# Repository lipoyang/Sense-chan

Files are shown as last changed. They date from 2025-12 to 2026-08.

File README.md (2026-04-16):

# ｾﾝｽﾁｬﾝ (Sense-chan)
ｾﾝｽﾁｬﾝはｽﾀｯｸﾁｬﾝ派生のSPRESENSEマイコン搭載ロボットです。  
SPRESENSE搭載のロボット用基板と対向2輪型ロボットおよびそのソフトウェアで構成されます。

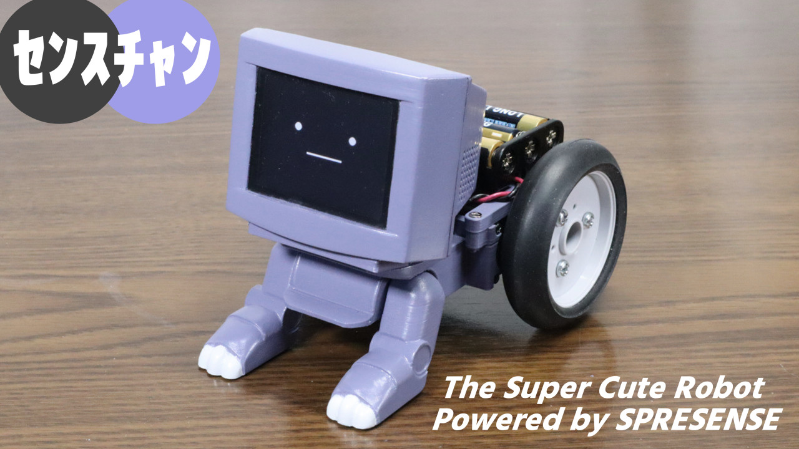
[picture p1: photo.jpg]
写真


## 解説

* [センスチャン ～ ｽﾀｯｸﾁｬﾝ派生のSPRESENSE搭載ロボット ～ by lipoyang | elchika](https://elchika.com/article/c5d4bbd1-0e7f-4fa6-907b-d6d020c664f9)

## ファイル
* [firmware](./firmware/) : ファームウェアのソースコード
* [mechanical](./mechanical/) : メカ部品のSTEPファイルとSTLファイル
* [board](./board/) : プリント基板の回路図とパターン設計

## SDカードにコピーするファイル

下記のファイルをマイクロSDカードにコピーして、ｾﾝｽﾁｬﾝのマイクロSDカードスロットに挿入してください。
* [fs_efont_ja_16.bin](./firmware/Sense-chan/sd_data/fs_efont_ja_16.bin) : フォントデータ
* [config.json](./firmware/Sense-chan/sd_data/config.json) : 設定ファイル

## 原典
このプロジェクトはｽﾀｯｸﾁｬﾝにインスパイアされた派生作品です。[ｽﾀｯｸﾁｬﾝ](https://github.com/stack-chan/stack-chan)は[ししかわ](https://x.com/stack_chan)さんが開発、公開している、 手乗りサイズのｽｰﾊﾟｰｶﾜｲｲコミュニケーションロボットです。

また、[B-SKY-Lab](https://x.com/eternalfriend17)さんが開発、公開している[ﾀｲﾘﾝﾁｬﾝ](https://github.com/kim-xps12/bsl-balancer)の機構設計やソフトウェアを一部参考にしています。

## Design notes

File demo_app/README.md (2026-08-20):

# デモ用Webアプリ
- ｾﾝｽﾁｬﾝのデモ用のWebアプリです。
- Web Bluetooth API に対応したChrome系のブラウザで動作します。
- iOS版のChromeには対応していません。
- UIのデザインに 源暎エムゴv2 フォントを使用しています。
- 源暎エムゴv2 フォントは SIL Open Font License 1.1 の下で提供されています。

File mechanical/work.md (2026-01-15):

# 作業メモ

## 3Dプリンタ出力
- 3Dプリンタ : Bambu Lab A1 mini
- フィラメント : PLA

## 追加工
- M2ネジの下穴はφ1.7で設計したが、3Dプリンタでは穴が細るので、ピンバイスを用いφ1.7のドリルでリワーク
- M3ネジの下穴はφ2.5で設計したが、3Dプリンタでは穴が細るので、ピンバイスを用いφ2.5のドリルでリワーク
- M2ネジのバカ穴は、細ることを見越してφ2.2で設計したがそれでも細いので、ピンバイスを用いφ2.0のドリルでリワーク
- 前脚の六角軸と本体の六角穴は、軸が太って穴が細ることを見越してマージンを設けたが、それでも嵌まらなかったので、六角軸を平ヤスリでリワーク
- 電池ボックスの固定穴(バカ穴)はネジ頭が電池に干渉するので、ボール盤を用いφ6.0のドリルで座グリ
- 電池ボックス固定プレートの本体取り付けネジはネジ頭が電池ボックスと干渉するので(設計ミス)、ボール盤を用いφ4.0で座グリして、皿ネジで取り付ける

## 表面処理と塗装
- 積層痕はヤスリがけでなるべく整形する
- いちじるしく段差が目立つ箇所についてはパテで埋めてヤスリがけ
- サーフェイサーを吹いて下地を整える
- 水性ホビーカラーで塗装
  - XHUG09 ミカエリス パープル
  - HUG104 ディアクティブ ホワイト 

## パネル
- デザインの都合でLCDパネルより筐体の開口部が大きいため、そのままでは見映えが悪い
- アクリサンデーの厚さ1mmの強化透明アクリル板を47mm×36mmにカット
- 裏面から黒枠を塗装し、透明部が42mm×32mmとなるようにする
- このパネルを筐体の開口部にはめ込む

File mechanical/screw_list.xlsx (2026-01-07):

使用箇所 | 個数 | 径 | 長さ | その他
ｾﾝｽﾁｬﾝ基板固定 | 4 | M2 | 4
頭部前後固定 | 4 | M2 | 5
首固定 | 2 | M2 | 8
前脚固定 | 2 | M2 | 4
前脚補強 | 2 | M2 | 15
電池ボックスプレート固定 | 4 | M2 | 8 | 皿ネジ
電池ボックス固定 | 2 | M3 | 5 | 皿ネジ
サーボ固定 | 8 | M2 | 8 | サーボの付属品
サーボホーン固定 | 8 | M2 | 6 | サーボの付属品
ホイール固定 | 6 | M3 | 8 | タイヤの付属品

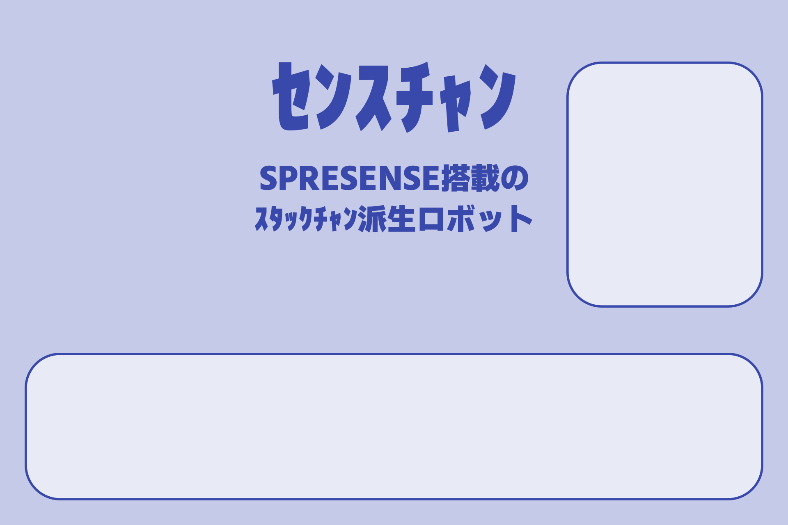
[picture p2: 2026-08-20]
demo_app/background.png

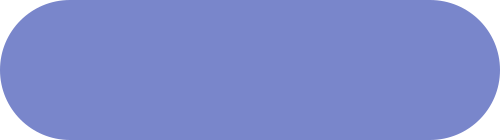
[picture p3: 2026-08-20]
demo_app/button_lowkey.png

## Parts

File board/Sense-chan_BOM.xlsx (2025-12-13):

Reference | Qty | Part Number | Description | Supplier | Supplier Code
C1, C3, C4, C6, C7, C9, C10, C11, C12, C14, C15, C16 | 12 | 0.1uF | 1608 (0603) | (在庫) | (generic)
C8, C17 | 1 | 1uF | 1608 (0603) | (在庫) | (generic)
C2, C5 | 2 | 22uF | 3216(1206) | (在庫) | (generic)
C13 | 1 | 47uF | 3216(1206) | (在庫) | (generic)
R1 | 1 | 62kΩ, class F | 1608 (0603) | digikey | 10-ERJ-U03F6202VCT-ND
R3 | 1 | 10kΩ, class F | 1608 (0603) | digikey | 10-ERJ-U03F1002VCT-ND
R2, R7 | 2 | 180kΩ | 1608 (0603) | (在庫) | (generic)
R4 | 1 | 10Ω | 1608 (0603) | (在庫) | (generic)
R5 | 1 | 47Ω | 1608 (0603) | (在庫) | (generic)
R6, R8, R9, R12 | 4 | 10kΩ | 1608 (0603) | (在庫) | (generic)
R10 | 1 | 100Ω | 1608 (0603) | (在庫) | (generic)
R11 | 1 | 2.2kΩ | 1608 (0603) | (在庫) | (generic)
RN1, RN2, RN3, RN4 | 4 | 1kΩ×4素子 EXB-38V102JV | 1608 (0603)×4素子, 凸型 | digikey | Y9102CT-ND
D1 | 1 | SS2040FL | D_SOD-123 | (在庫, 秋月) | 102073
J1, J7 | 2 | B3B-EH-A | 日圧EH3ピン(トップ型) | (在庫, 共立) | 5CP14I
J2 | 1 | LCD Flexible Cable | 0.8mmピッチ 12ピン | - | -
J3 | 1 | DF40HC(3.0)-100DS-0.4V | SPRESENSE B2Bコネクタ | digikey | 26-DF40HC(3.0)-100DS-0.4V(51)CT-ND
J4 | 1 | DM3AT | ヒロセ microSDカードスロット | digikey | 26-DM3AT-SF-PEJM5(11)CT-ND
J5, J6 | 2 | B4B-EH-A | 日圧EH4ピン(トップ型) | (在庫, 共立) | 5CP14J
Q1 | 1 | IRFML8244TRPBF | SOT-23 | (在庫, digikey) | IRFML8244TRPBFCT-ND
U1 | 1 | TC1262-3.3VDB | SOT-223-3_TabPin2 | (在庫, digikey) | TC1262-3.3VDB-ND
U2, U3 | 2 | LSF0108PWR | PW0020A | digikey | 296-37828-1-ND
U4 | 1 | SN74LV1T126DBVR | SOT-23-5 | digikey | 296-37174-1-ND
U5 | 1 | SN74LV1T125DBVR | SOT-23-5 | digikey | 296-37172-1-ND

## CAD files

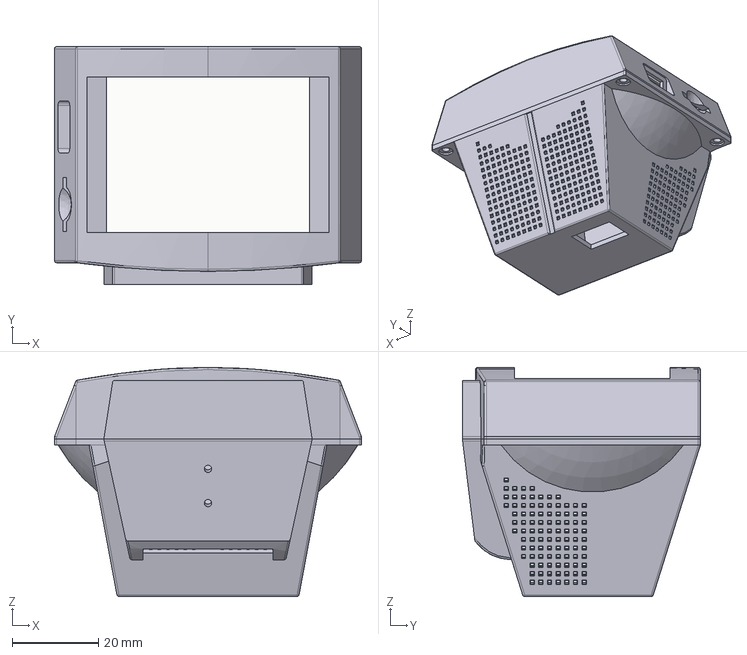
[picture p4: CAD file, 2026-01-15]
mechanical/STEP/VaioMonitor.step
71.0 x 55.0 x 53.0 mm

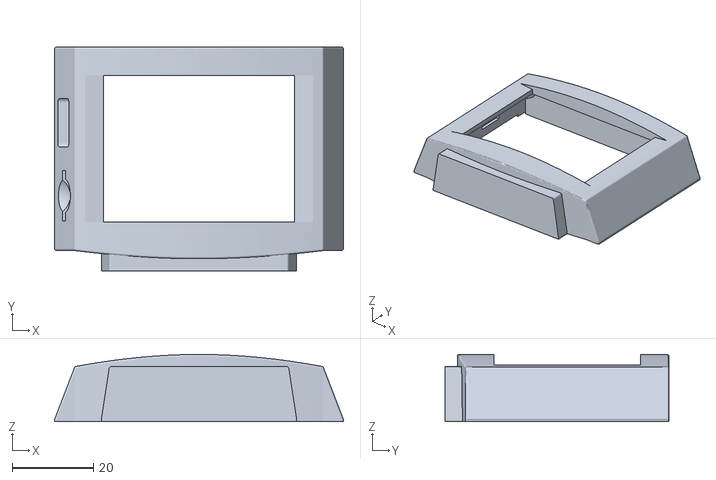
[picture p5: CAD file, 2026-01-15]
mechanical/STL/VaioMonitor_frame.stl
71.0 x 55.0 x 16.5

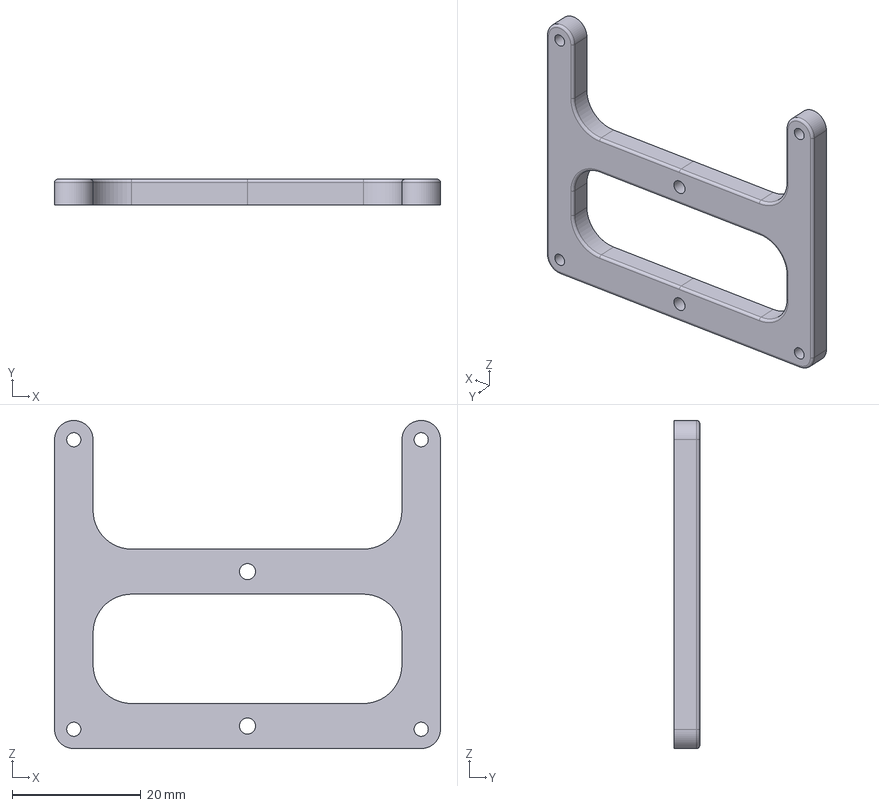
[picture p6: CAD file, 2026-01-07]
mechanical/STEP/RearPlate.step
60.0 x 4.00 x 51.0 mm

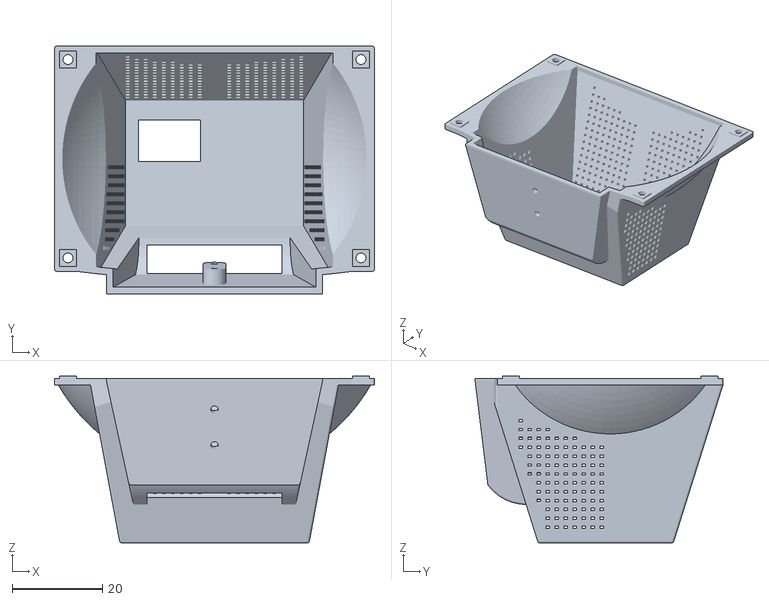
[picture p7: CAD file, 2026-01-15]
mechanical/STL/VaioMonitor_back.stl
71.0 x 55.0 x 37.0

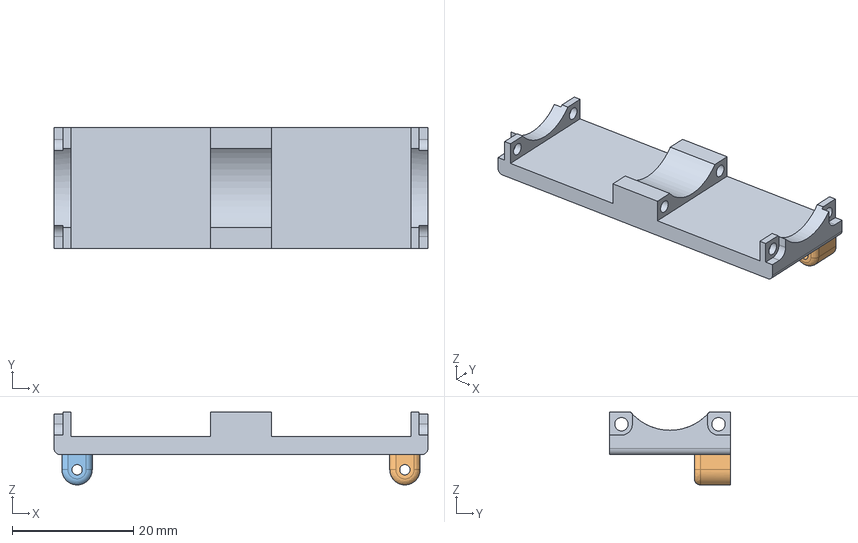
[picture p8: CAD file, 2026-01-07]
mechanical/STEP/RearBracket.step
61.6 x 20.0 x 12.0 mm

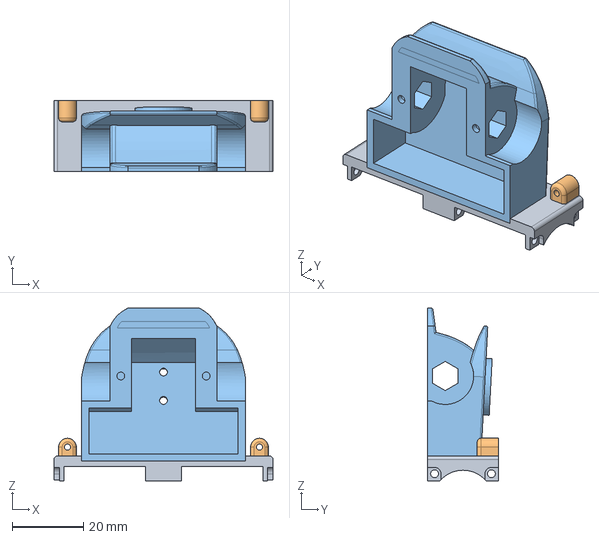
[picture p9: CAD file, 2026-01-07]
mechanical/STEP/Body.step
61.6 x 20.0 x 48.6 mm

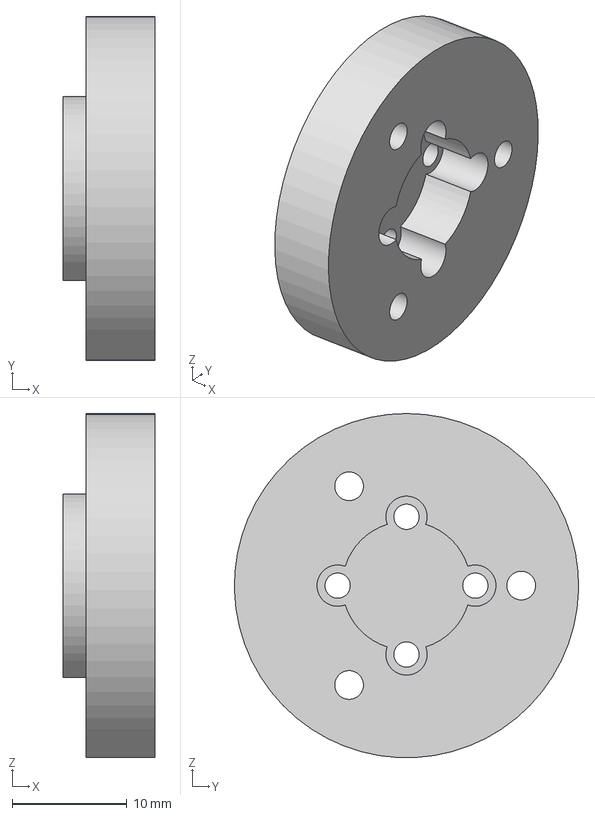
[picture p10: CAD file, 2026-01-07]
mechanical/STEP/WheelAdaptor.step
8.00 x 30.0 x 30.0 mm

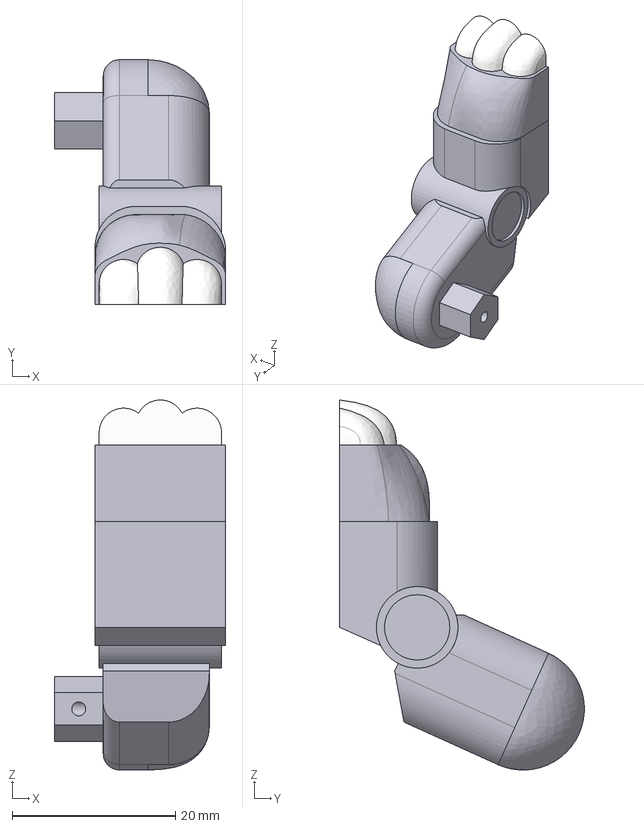
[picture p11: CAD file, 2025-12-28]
mechanical/STEP/LegL.step
21.0 x 30.0 x 45.4 mm

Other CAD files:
mechanical/STEP/LegR.step
mechanical/STL/Body.stl
mechanical/STL/LegL.stl
mechanical/STL/LegR.stl
mechanical/STL/RearBracket.stl
mechanical/STL/RearPlate.stl
mechanical/STL/WheelAdaptor.stl
mechanical/Sense-chan.f3d

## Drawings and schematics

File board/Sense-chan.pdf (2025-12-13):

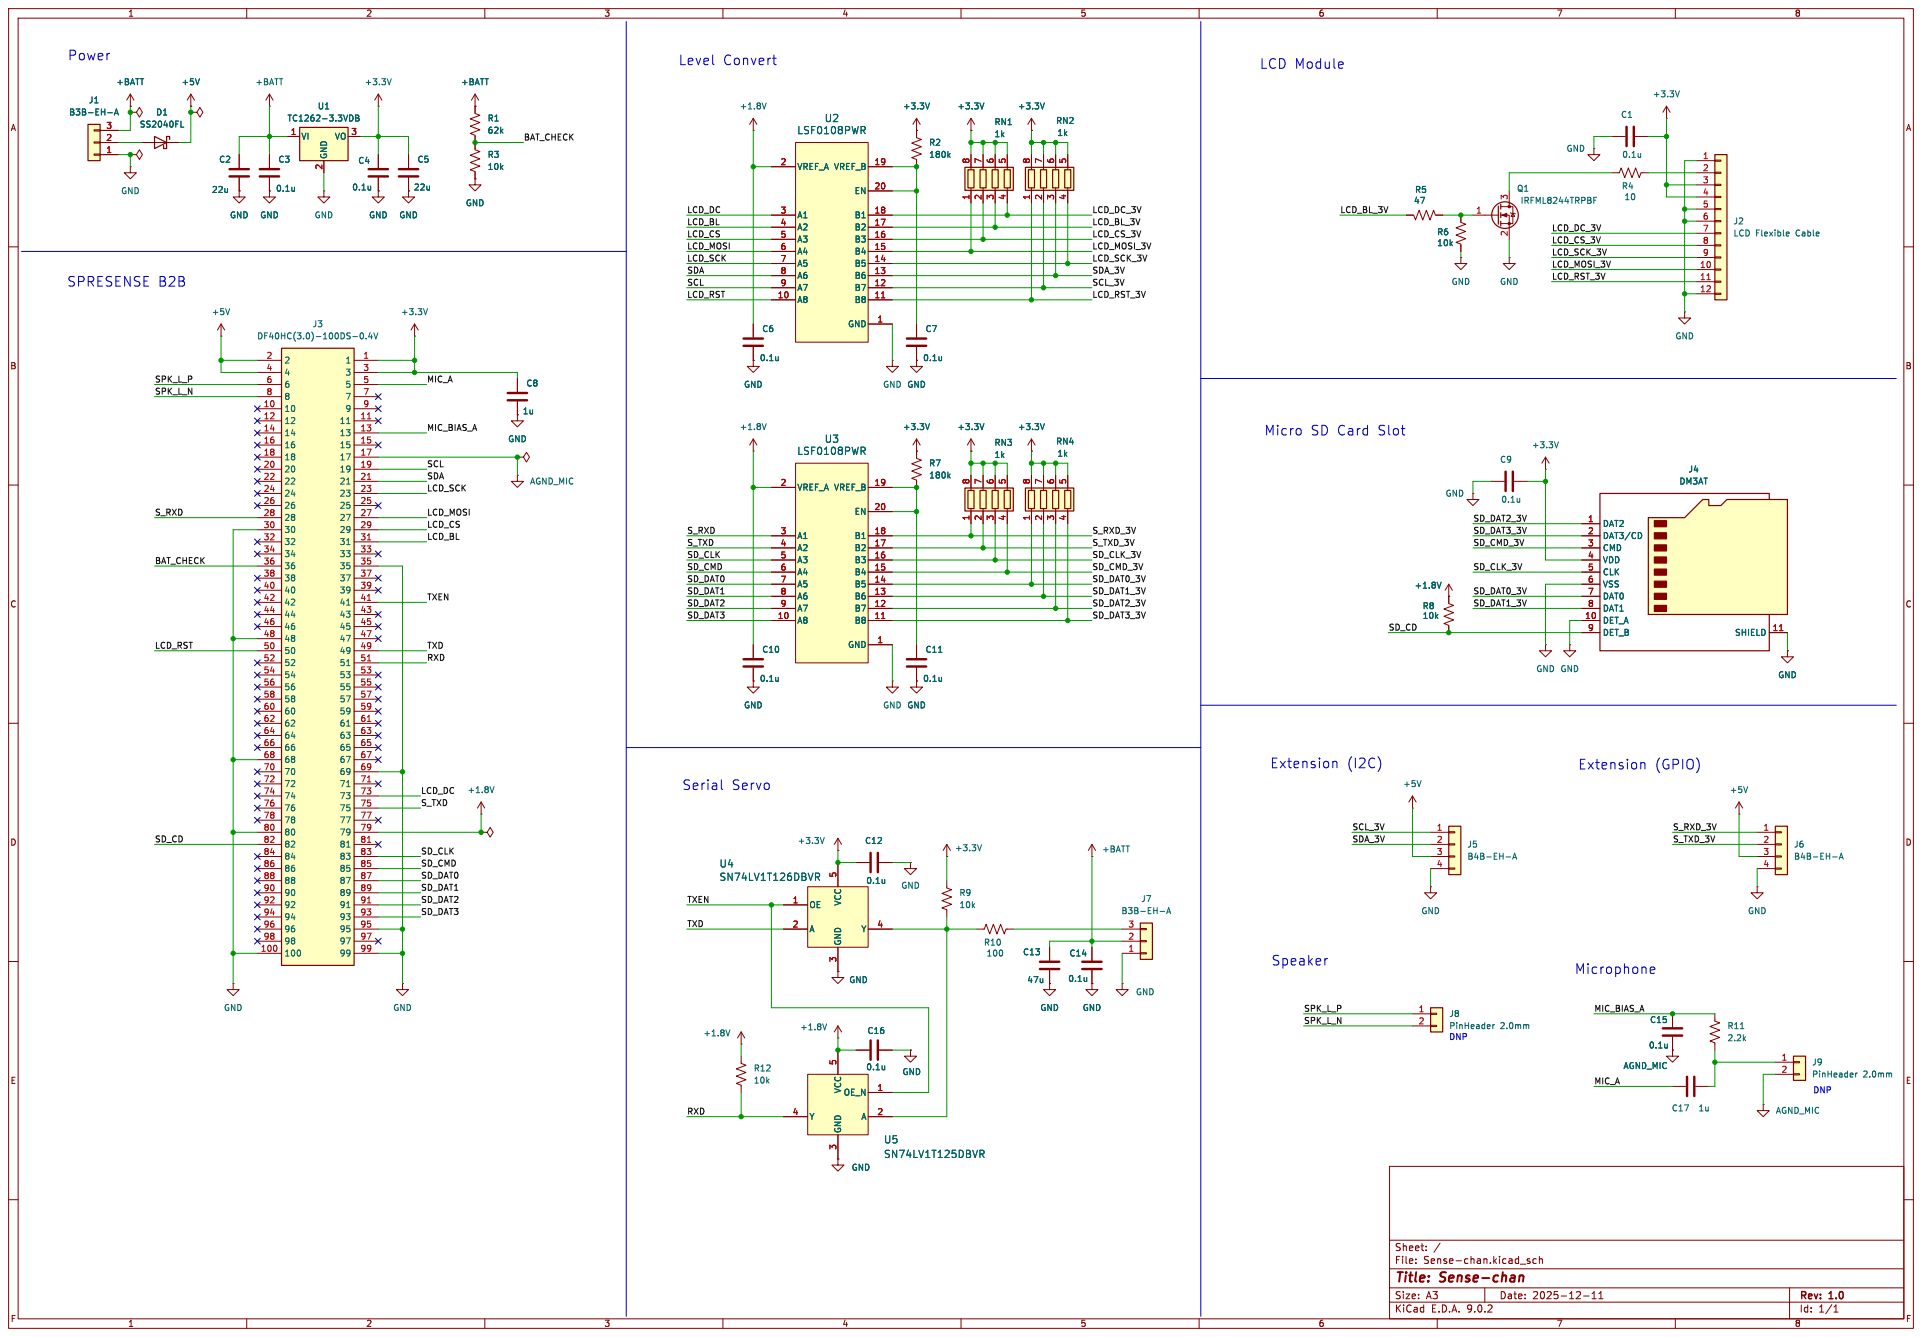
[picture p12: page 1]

Micro SD Card Slot

Extension (GPIO) DNP Speaker

File: Sense-chan.kicad_sch Sheet: /
Id: 1/1 Title: Sense-chan

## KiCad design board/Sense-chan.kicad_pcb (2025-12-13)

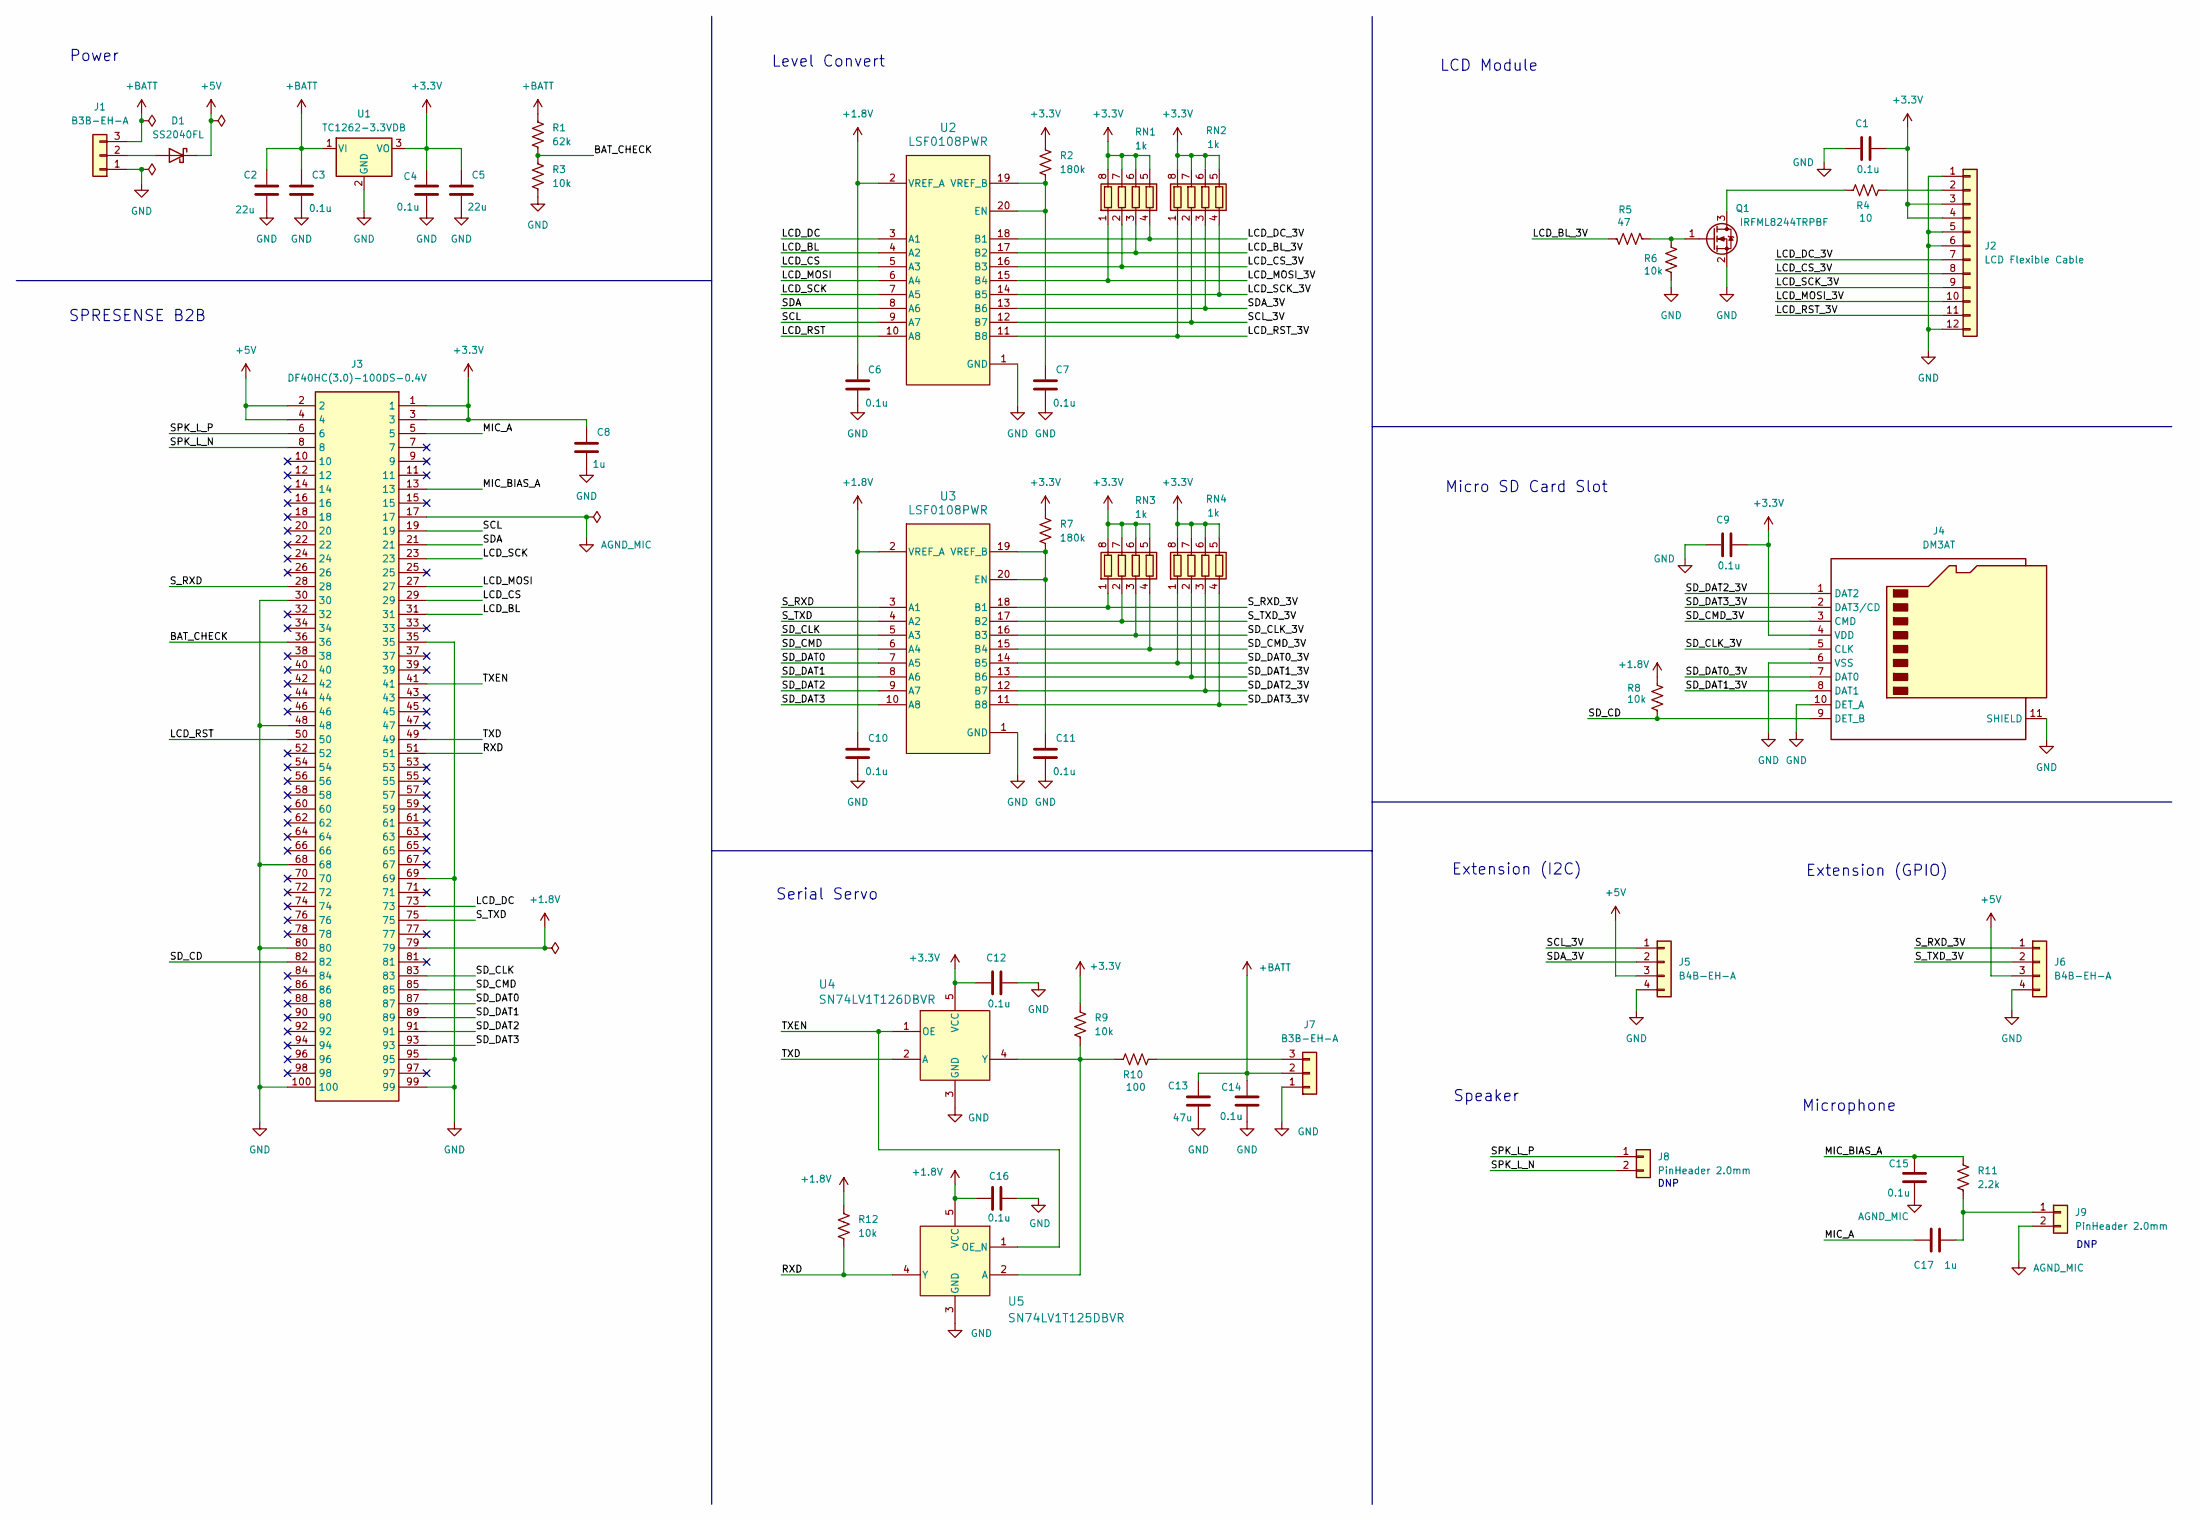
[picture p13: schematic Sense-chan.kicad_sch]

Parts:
C1, C3, C4, C6, C7, C9, C10, C11, C12, C14, C15, C16: 0.1u; C_0603_1608Metric; LCSC C14663
C2, C5: 22u; C_1206_3216Metric
C8: 1u; C_0603_1608Metric
C13: 47u; C_1206_3216Metric
C17: 1u; C_0603_1608Metric; LCSC C14663
D1: SS2040FL; D_SOD-123
J1, J7: B3B-EH-A; JST_EH_B3B-EH-A_1x03_P2.50mm_Vertical
J2: LCD Flexible Cable; LCD-Flex12-0.8mm
J3: DF40HC(3.0)-100DS-0.4V; spresense; Manufacturer_Part_Number DF40HC(3.0)-100DS-0.4V(51)
J4: DM3AT; microSD_HC_Hirose_DM3AT-SF-PEJM5
J5, J6: B4B-EH-A; JST_EH_B4B-EH-A_1x04_P2.50mm_Vertical
J8, J9: PinHeader 2.0mm; PinHeader_1x02_P2.00mm_Vertical
Q1: IRFML8244TRPBF; SOT-23
R1: 62k; R_0603_1608Metric
R2, R7: 180k; R_0603_1608Metric
R3, R6, R8, R9, R12: 10k; R_0603_1608Metric
R4: 10; R_0603_1608Metric
R5: 47; R_0603_1608Metric
R10: 100; R_0603_1608Metric
R11: 2.2k; R_0603_1608Metric
RN1, RN2, RN3, RN4: 1k; R_Array_Convex_4x0603
U1: TC1262-3.3VDB; SOT-223-3_TabPin2
U2, U3: LSF0108PWR; PW0020A
U4: SN74LV1T126DBVR; SOT-23-5
U5: SN74LV1T125DBVR; SOT-23-5

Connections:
+1.8V: C6.1, C10.1, C16.1, J3.79, R8.1, R12.1, U2.2 (VREF_A), U3.2 (VREF_A), U5.5 (VCC)
+3.3V: C1.2, C4.1, C5.1, C8.1, C9.2, C12.1, J2.3, J2.4, J3.1, J3.3, J4.4 (VDD), R2.1, R7.1, R9.1, RN1.5 (R4.2), RN1.6 (R3.2), RN1.7 (R2.2), RN1.8 (R1.2), RN2.5 (R4.2), RN2.6 (R3.2), RN2.7 (R2.2), RN2.8 (R1.2), RN3.5 (R4.2), RN3.6 (R3.2), RN3.7 (R2.2), RN3.8 (R1.2), RN4.5 (R4.2), RN4.6 (R3.2), RN4.7 (R2.2), RN4.8 (R1.2), U1.3 (VO), U4.5 (VCC)
+5V: D1.1 (K), J3.2, J3.4, J5.3, J6.3
+BATT: C2.1, C3.1, C13.1, C14.1, J1.3, J7.2, R1.1, U1.1 (VI)
/BAT_CHECK: J3.36, R1.2, R3.1
/LCD_BL: J3.31, U2.4 (A2)
/LCD_BL_3V: R5.1, RN1.3 (R3.1), U2.17 (B2)
/LCD_CS: J3.29, U2.5 (A3)
/LCD_CS_3V: J2.8, RN1.2 (R2.1), U2.16 (B3)
/LCD_DC: J3.73, U2.3 (A1)
/LCD_DC_3V: J2.7, RN1.4 (R4.1), U2.18 (B1)
/LCD_MOSI: J3.27, U2.6 (A4)
/LCD_MOSI_3V: J2.10, RN1.1 (R1.1), U2.15 (B4)
/LCD_RST: J3.50, U2.10 (A8)
/LCD_RST_3V: J2.11, RN2.1 (R1.1), U2.11 (B8)
/LCD_SCK: J3.23, U2.7 (A5)
/LCD_SCK_3V: J2.9, RN2.4 (R4.1), U2.14 (B5)
/MIC_A: C17.1, J3.5
/MIC_BIAS_A: C15.1, J3.13, R11.1
/RXD: J3.51, R12.2, U5.4 (Y)
/SCL: J3.19, U2.9 (A7)
/SCL_3V: J5.1, RN2.2 (R2.1), U2.12 (B7)
/SDA: J3.21, U2.8 (A6)
/SDA_3V: J5.2, RN2.3 (R3.1), U2.13 (B6)
/SD_CD: J3.82, J4.9 (DET_B), R8.2
/SD_CLK: J3.83, U3.5 (A3)
/SD_CLK_3V: J4.5 (CLK), RN3.3 (R3.1), U3.16 (B3)
/SD_CMD: J3.85, U3.6 (A4)
/SD_CMD_3V: J4.3 (CMD), RN3.4 (R4.1), U3.15 (B4)
/SD_DAT0: J3.87, U3.7 (A5)
/SD_DAT0_3V: J4.7 (DAT0), RN4.1 (R1.1), U3.14 (B5)
/SD_DAT1: J3.89, U3.8 (A6)
/SD_DAT1_3V: J4.8 (DAT1), RN4.2 (R2.1), U3.13 (B6)
/SD_DAT2: J3.91, U3.9 (A7)
/SD_DAT2_3V: J4.1 (DAT2), RN4.3 (R3.1), U3.12 (B7)
/SD_DAT3: J3.93, U3.10 (A8)
/SD_DAT3_3V: J4.2 (DAT3/CD), RN4.4 (R4.1), U3.11 (B8)
/SPK_L_N: J3.8, J8.2
/SPK_L_P: J3.6, J8.1
/S_RXD: J3.28, U3.3 (A1)
/S_RXD_3V: J6.1, RN3.1 (R1.1), U3.18 (B1)
/S_TXD: J3.75, U3.4 (A2)
/S_TXD_3V: J6.2, RN3.2 (R2.1), U3.17 (B2)
/TXD: J3.49, U4.2 (A)
/TXEN: J3.41, U4.1 (OE), U5.1 (OE_N)
AGND_MIC: C15.2, J3.17, J9.2
GND: C1.1, C2.2, C3.2, C4.2, C5.2, C6.2, C7.2, C8.2, C9.1, C10.2, C11.2, C12.2, C13.2, C14.2, C16.2, J1.1, J2.1, J2.5, J2.6, J2.12, J3.30, J3.35, J3.48, J3.68, J3.69, J3.80, J3.95, J3.99, J3.100, J4.6 (VSS), J4.10 (DET_A), J4.11 (SHIELD), J5.4, J6.4, J7.1, Q1.2 (S), R3.2, R6.2, U1.2 (GND), U2.1 (GND), U3.1 (GND), U4.3 (GND), U5.3 (GND)
unnamed: D1.2 (A), J1.2
unnamed: J2.2, R4.2
unnamed: J7.3, R10.2
unnamed: C17.2, J9.1, R11.2
unnamed: Q1.3 (D), R4.1
unnamed: Q1.1 (G), R5.2, R6.1
unnamed: C7.1, R2.2, U2.19 (VREF_B), U2.20 (EN)
unnamed: C11.1, R7.2, U3.19 (VREF_B), U3.20 (EN)
unnamed: R9.2, R10.1, U4.4 (Y), U5.2 (A)

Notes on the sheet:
Extension (I2C)
Serial Servo
Micro SD Card Slot
Speaker
SPRESENSE B2B
Extension (GPIO)
DNP
Microphone
Level Convert
Power
LCD Module

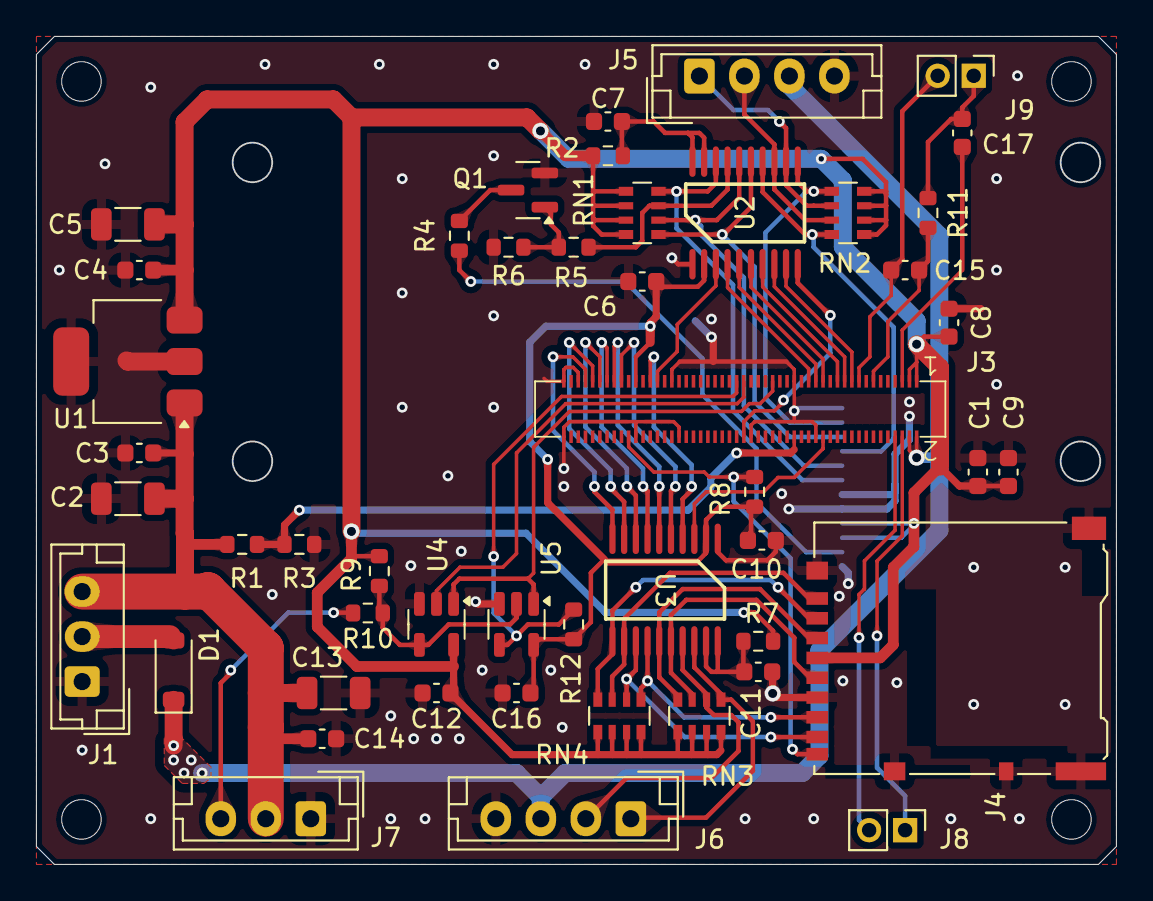
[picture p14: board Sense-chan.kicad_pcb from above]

Board: 2 copper layers, 60.0 x 46.0 mm, 49 parts (1 on the bottom side), 56 nets.

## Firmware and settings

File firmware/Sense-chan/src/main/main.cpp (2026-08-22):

#ifdef SUBCORE
#error "Core selection is wrong!!"
#endif

#include <Arduino.h>
#include "SenseChanFace.h"
#include "Motor.h"
#include "BleReceiver.h"
#include "BatteryCheck.h"
#include "SdCard.h"
#include "SerialCmd.h"
#include "VoiceDetector.h"

// スタックチャンの顔表示器
SenseChanFace face;
// モータ制御
Motor motor;
// BLEラジコン受信器
BleReceiver receiver;
// バッテリー電圧監視
BatteryCheck batteryCheck;
// 音声コマンド検出器
VoiceDetector vd;
// SDカード
SdCard sdCard;
// USBシリアルコマンド (開発用)
SerialCmd serialCmd;

// BLEラジコン接続時
void onConnect()
{
  Serial.println("Connected!");

#ifdef USE_PROPO_APP  
  face.setMicroMotion(false);
  face.setBaseExpression(Expression::Neutral);
  face.setExpression(Expression::Happy, 2000);
  face.setSpeachText("プロポ接続したよ", 2000);

  // DYNAMIXELシリアルサーボを速度制御に変更
  motor.setVelocityMode();
#else
  face.setMicroMotion(true);
  face.setBaseExpression(Expression::Neutral);
  face.setExpression(Expression::Happy, 2000);
  face.setSpeachText("アプリと接続したよ", 2000);

  // うろちょろモードに設定
  motor.setMode(MODE_UROCHORO);
#endif
}

// BLEラジコン切断時
void onDisconnect()
{
  Serial.println("Disconnected!");

#ifdef USE_PROPO_APP  
  face.setBaseExpression(Expression::Neutral); // Sleepy);
  face.setExpression(Expression::Neutral, 2000);
  face.setSpeachText("プロポ切断したよ", 2000);
  face.setMicroMotion(true);

  // DYNAMIXELシリアルサーボを位置制御に変更
  motor.setPositionMode();
#else
  face.setBaseExpression(Expression::Neutral);
  face.setExpression(Expression::Neutral, 2000);
  face.setSpeachText("アプリと切断したよ", 2000);
  face.setMicroMotion(true);

  // うろちょろモードに設定
  motor.setMode(MODE_UROCHORO);
#endif
}

// BLEラジコン受信時
void onReceive(int l, int r)
{
  Serial.printf("Received: l=%d r=%d\n", l, r);

  // モータの速度制御
  motor.setVelocity((float)l, (float)r);
}

// モード設定受信時 (デモアプリ用)
void onSetMode(int mode)
{
  Serial.printf("Set Mode: mode=%d\n", mode);

  switch(mode){
    case MODE_UROCHORO:
      face.setMicroMotion(true);
      face.setBaseExpression(Expression::Neutral);
      face.setExpression(Expression::Happy, 2000);
      face.setSpeachText("うろちょろモード！", 2000);
      break;
    case MODE_RADIDON:
      face.setMicroMotion(false);
      face.setBaseExpression(Expression::Neutral);
      face.setExpression(Expression::Happy, 2000);
      face.setSpeachText("ラジコンモード！", 2000);
      break;
    case MODE_GYRO:
      face.setMicroMotion(false);
      face.setMicroMotion(false);
      face.setBaseExpression(Expression::Neutral);
      face.setExpression(Expression::Happy, 2000);
      face.setSpeachText("ジャイロモード！", 2000);
      break;
  }

  motor.setMode(mode);
}

// バッテリー電圧監視コールバック
void onBatteryCheck(float voltage, bool wasLowBattery)
{
  // Serial.printf("Battery Voltage: %.2f V\n", voltage);
  receiver.sendStatus((int)(voltage * 1000.0f), motor.getStatus());

  if(voltage < LOW_BATTERY) {
    face.setExpression(Expression::Sad, 2000);
    face.setSpeachText("電圧が下がってるよ", 2000);
  }else if(wasLowBattery) {
    face.setExpression(Expression::Neutral, 2000);
    face.clearSpeachText();
  }
}

// スタックチャンの微動コールバック
void onMicroMotion(float x, float y)
{
  // Serial.printf("MicroMotion: x=%.2f y=%.2f\n", x, y);
  
  // モータの位置制御  
  motor.setPosition(x, y);
}

// シリアルコマンド (開発用)
void onCommand(int argc, char const *argv[])
{
  if(argc <= 0) return;

  // パラメータ設定
  if(strcmp(argv[0], "set") == 0 && argc == 3)
  {
    if(strcmp(argv[1], "Kx") == 0) {
      motor.parameter.Kx = atof(argv[2]);
      motor.setParameter();
      Serial.printf("Set Kx = %.2f\n", motor.parameter.Kx);
    }
    else if(strcmp(argv[1], "Ky") == 0) {
      motor.parameter.Ky = atof(argv[2]);
      motor.setParameter();
      Serial.printf("Set Ky = %.2f\n", motor.parameter.Ky);
    }
    else if(strcmp(argv[1], "Vmax") == 0) {
      motor.parameter.Vmax = atof(argv[2]);
      motor.setParameter();
      Serial.printf("Set Vmax = %.2f\n", motor.parameter.Vmax);
    }
    else if(strcmp(argv[1], "Vfull") == 0) {
      motor.parameter.Vfull = atof(argv[2]);
      motor.setParameter();
      Serial.printf("Set Vfull = %.2f\n", motor.parameter.Vfull);
    }
    else if(strcmp(argv[1], "Kp") == 0) {
      motor.parameter.Kp = atof(argv[2]);
      motor.setParameter();
      Serial.printf("Set Kp = %.2f\n", motor.parameter.Kp);
    }
    else if(strcmp(argv[1], "Ki") == 0) {
      motor.parameter.Ki = atof(argv[2]);
      motor.setParameter();
      Serial.printf("Set Ki = %.2f\n", motor.parameter.Ki);
    }
    else if(strcmp(argv[1], "Kd") == 0) {
      motor.parameter.Kd = atof(argv[2]);
      motor.setParameter();
      Serial.printf("Set Kd = %.2f\n", motor.parameter.Kd);
    }
  }
  // パラメータ表示
  else if(strcmp(argv[0], "print") == 0 && argc == 1)
  {
    Serial.printf("Kx=%.2f Ky=%.2f Vmax=%.2f Vfull=%.2f Kp=%.2f Ki=%.2f Kd=%.2f\n",
    motor.parameter.Kx, motor.parameter.Ky, motor.parameter.Vmax, motor.parameter.Vfull,
    motor.parameter.Kp, motor.parameter.Ki, motor.parameter.Kd);
  }
  // パラメータ保存
  else if(strcmp(argv[0], "save") == 0 && argc == 1)
  {
    sdCard.Kx = motor.parameter.Kx;
    sdCard.Ky = motor.parameter.Ky;
    sdCard.Vmax = motor.parameter.Vmax;
    sdCard.Vfull = motor.parameter.Vfull;
    sdCard.Kp = motor.parameter.Kp;
    sdCard.Ki = motor.parameter.Ki;
    sdCard.Kd = motor.parameter.Kd;
    if(sdCard.save()) {
      Serial.println("Settings saved to SD card.");
    } else {
      Serial.println("Failed to save settings to SD card.");
    }
  }
  // おすわり
  else if(strcmp(argv[0], "sit") == 0 && argc == 1)
  {
    motor.setPause(true);
    Serial.println("Sit down!");
  }
  // おすわり解除
  else if(strcmp(argv[0], "ok") == 0 && argc == 1)
  {
    motor.setPause(false);
    Serial.println("OK!");
  }
  // 音声コマンド登録
  else if(strcmp(argv[0], "regist") == 0 && argc == 2)
  {
    int command_no = atoi(argv[1]);
    if(command_no >=0 && command_no <= 4){
      Serial.printf("Voice command [%d] registing...\n", command_no);
      vd.regist(command_no);
    }else{
      Serial.printf("Bad voice command number (%d)\n", command_no);
    }
  }
  // 音声コマンド検出
  else if(strcmp(argv[0], "detect") == 0 && argc == 1)
  {
    Serial.println("Voice command detecting...");
      vd.detect();
  }
  // 音声コマンド登録/検出のキャンセル
  else if(strcmp(argv[0], "cancel") == 0 && argc == 1)
  {
    Serial.println("Voice command canceled!");
      vd.cancel();
  }
  else{
    Serial.println("unknown command");
  }
}

// 音声コマンド登録通知
void onRegist(uint32_t commnad_no)
{
  if(commnad_no < MAX_COMMAND){
    printf("Voice Command Registed! (%ld)\n", commnad_no);
  }else{
    printf("Voice Command Regist ERROR! (%ld)\n", commnad_no);
  }
}

// 音声コマンド検出通知
void onDetect(uint32_t commnad_no)
{
  if(commnad_no < MAX_COMMAND){
    printf("Voice Command Detected! (%ld)\n", commnad_no);
  }else if(commnad_no == MFCC_MISMATCH){
    printf("Voice Command mismatch\n");
  }else{
    printf("Voice Command Detect ERROR! (%ld)\n", commnad_no);
  }
}

// 初期化
void setup()
{
  serialCmd.onCommand = onCommand;
  serialCmd.begin();

  // SDカードの初期化と設定読み込み
  if(sdCard.begin()){
    sdCard.load();
    motor.parameter.Kx   = sdCard.Kx;
    motor.parameter.Ky   = sdCard.Ky;
    motor.parameter.Vmax = sdCard.Vmax;
    motor.parameter.Vfull = sdCard.Vfull;
    motor.parameter.Kp   = sdCard.Kp;
    motor.parameter.Ki   = sdCard.Ki;
    motor.parameter.Kd   = sdCard.Kd;
    face.pwmBL = sdCard.PWM;
    receiver.RX = sdCard.RX;
    receiver.TX = sdCard.TX;
    receiver.Baud = sdCard.Baud;
  }

  // DYNAMIXELシリアルサーボの初期化 (位置制御)
  motor.begin();
  
  // BLEラジコン受信器の初期化
  receiver.onConnect = onConnect;
  receiver.onDisconnect = onDisconnect;
  receiver.onReceive = onReceive;
  receiver.onSetMode = onSetMode;
  receiver.begin();

  // スタックチャンの顔の初期化
  face.onMicroMotion = onMicroMotion;
  face.begin();
  face.setBaseExpression(Expression::Neutral); // Sleepy);
  face.setExpression(Expression::Happy, 2000);
  face.setMicroMotion(true);

  // バッテリー電圧監視の初期化
  batteryCheck.begin();
  batteryCheck.onBatteryCheck = onBatteryCheck;

  // 音声コマンド検出器の初期化
  //vd.onRegist = onRegist;
  //vd.onDetect = onDetect;
  //vd.begin();
}

// メインループ
void loop()
{
  // BLEラジコン受信器
  receiver.loop();
  // スタックチャンの顔
  face.loop();
  // バッテリー電圧監視
  batteryCheck.loop();
  // モータ制御
  motor.loop();
  // シリアルコマンド受信
  serialCmd.loop();
  // 音声コマンド検出器
  //vd.loop();

  usleep(1000);
}

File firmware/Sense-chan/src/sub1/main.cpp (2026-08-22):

#if (SUBCORE != 1)
#error "Core selection is wrong!!"
#endif

#include <Arduino.h>
#include <MP.h>
#include <Dynamixel2Arduino.h>
#include "IMU.h"
#include "PollingTimer.h"

// メインコアID
const int MAINCORE_ID = 0;

// メッセージID定義
const int8_t MSGID_BEGUN = 1;
const int8_t MSGID_SET_PARAMETER = 2;
const int8_t MSGID_SET_VELOCITY_MODE = 3;
const int8_t MSGID_SET_POSITION_MODE = 4;
const int8_t MSGID_SET_VELOCITY = 5;
const int8_t MSGID_SET_POSITION = 6;
const int8_t MSGID_SET_PAUSE = 7;
const int8_t MSGID_SET_MODE = 8;

// モード
#define MODE_UROCHORO   0 // うろちょろ
#define MODE_RADIDON    1 // ラジコン
#define MODE_GYRO       2 // ジャイロ

// DYNAMIXEL設定
#define DXL_SERIAL   Serial2  // シリアルポート
const int DXL_DIR_PIN = 5;    // 半二重通信の方向制御ピン
const uint8_t DXL_ID[2] = {1, 2} ;   // 左右のモータID
const float DXL_PROTOCOL_VERSION = 2.0; // プロトコルバージョン
Dynamixel2Arduino dxl(DXL_SERIAL, DXL_DIR_PIN);
using namespace ControlTableItem;

// モータ制御関連
IntervalTimer servoTimer;     // 周期タイマ
int servoMode = OP_POSITION;  // 制御モード
float posOffset[2] = {0.0f, 0.0f}; // 位置オフセット
float posTarget[2] = {0.0f, 0.0f}; // 目標値
float posCurrent[2] = {0.0f, 0.0f}; // 現在値
float Kx = 120.0f;  // 旋回成分の係数 [度]
float Ky = 60.0f;   // 並進成分の係数 [度]
float Vmax = 2.0f;  // 位置制御の台形制御の最大速度
float Vfull = 12.0f; // 速度制御の最大速度 [%]
float Kp = 0.25f;  // PID制御の比例ゲイン
float Ki = 0.0f;   // PID制御の積分ゲイン
float Kd = 0.25f;  // PID制御の微分ゲイン
bool pausing = false; // 一時停止中か？
float ie = 0.0f; // PID制御の積分値
int mode = MODE_UROCHORO; // モード

// IMUセンサ関連
IMU imu;

// エラーループ
void errorLoop(int num)
{
  int i;
  while (1) {
    for (i = 0; i < num; i++) {
      digitalWrite(LED1, HIGH);
      delay(300);
      digitalWrite(LED1, LOW);
      delay(300);
    }
    delay(1000);
  }
}

// モータ制御
void servoControl()
{
  if(pausing) return; // 一時停止中

  // 位置制御モードか？
  if(servoMode == OP_POSITION)
  {
    for(uint8_t i = 0; i < 2; i++) {
      uint8_t id = DXL_ID[i];

      float diff = posTarget[i] - posCurrent[i];
      if (diff >  Vmax) diff =  Vmax;
      if (diff < -Vmax) diff = -Vmax;
      posCurrent[i] += diff;
      dxl.setGoalPosition(id, posOffset[i] + posCurrent[i], UNIT_DEGREE);
    }
  }
  // 速度制御モードか？
  else if(servoMode == OP_VELOCITY)
  {
    // ジャイロモードか？
    if(mode == MODE_GYRO){
      // 方位角の取得
      float theta = imu.getTheta();
      float gyro = imu.getGyro();
      static int cnt = 0;

      // 速度制御モード
      if(theta > 5.0f || theta < -5.0f) {
        ie = 0.0f; // 積分値をリセット (Anti-windup)
      }else{
        ie += theta;
      }

      float v =  -Kp * theta - Ki * ie - Kd * gyro;
      dxl.setGoalVelocity(DXL_ID[0], v, UNIT_PERCENT);
      dxl.setGoalVelocity(DXL_ID[1], v, UNIT_PERCENT);

      if(++cnt >= 50) {
        cnt = 0;
        // MPLog("theta=%.2f, v=%.2f, ie=%.2f, gyro=%.2f\n", theta, v, ie, gyro);
      }
    }
  }
}

// 初期化
void setup()
{
  // サブコア開始
  int ret = MP.begin();
  if (ret < 0) {
    errorLoop(2);
  }

  // DYNAMIXELシリアルサーボの初期化 (位置制御)
  dxl.begin(57600);
  dxl.setPortProtocolVersion(DXL_PROTOCOL_VERSION);
  for(uint8_t i = 0; i < 2; i++) {
    uint8_t id = DXL_ID[i];
    dxl.ping(id);
    dxl.torqueOff(id);
  //dxl.setOperatingMode(id, OP_POSITION);
    dxl.setOperatingMode(id, OP_EXTENDED_POSITION);
    posOffset[i] = dxl.getPresentPosition(id, UNIT_DEGREE);
  //MPLog("Offset[%d] = %f\n", i, posOffset[i] );
    posTarget[i] = 0.0f;
    posCurrent[i] = 0.0f;
    dxl.setGoalPosition(id, posOffset[i], UNIT_DEGREE);
    dxl.torqueOn(id);
  }
  servoMode = OP_POSITION;

  // IMUセンサの初期化
  if(!imu.begin()){
    MPLog("IMU: begin error");
    // errorLoop(3);
  }else{
    imu.calibrate(); // キャリブレーション開始
  }
  
  // 初期化完了をメインコアに知らせる
  uint32_t status = (imu.isError()) ? 0x0001 : 0x0000;
  MP.Send(MSGID_BEGUN, status, MAINCORE_ID);

  // パラメータ設定
  MP.RecvTimeout(MP_RECV_BLOCKING);
  int8_t msgid;
  uint32_t dummy = 0;
  struct Parameter{
    float Kx;   // 旋回成分の係数 [度]
    float Ky;   // 並進成分の係数 [度]
    float Vmax; // // 位置制御の台形制御の最大速度
    float Vfull; // 速度制御の最大速度 [%]
    float Kp;   // PID制御の比例ゲイン
    float Ki;   // PID制御の積分ゲイン
    float Kd;   // PID制御の微分ゲイン
  };
  Parameter* pParam;
  MP.Recv(&msgid, &pParam);
  if (msgid != MSGID_SET_PARAMETER) {
      MPLog("Motor: MP.Recv error: no SET_PARAMETER message %d\n", msgid);
  }
  Kx = pParam->Kx;
  Ky = pParam->Ky;
  Vmax = pParam->Vmax;
  Vfull = pParam->Vfull;
  Kp = pParam->Kp;
  Ki = pParam->Ki;
  Kd = pParam->Kd;
  MP.Send(MSGID_SET_PARAMETER, dummy, MAINCORE_ID);

  MP.RecvTimeout(MP_RECV_POLLING);

  // モータ制御用タイマ
  servoTimer.set(20);
}

// メインループ
void loop()
{
  // メッセージID
  int8_t msgid;

  // メッセージデータ
  typedef struct {
      float l;
      float r;
  } S_Velocity;

  typedef struct {
      float x;
      float y;
  } S_Position;

  typedef struct{
    float Kx;
    float Ky;
    float Vmax;
    float Vfull;
    float Kp;
    float Ki;
    float Kd;
  } S_Parameter;

  typedef struct{
    bool pause;
  } S_Pause;

  typedef struct {
    int mode;
  } S_SetMode;

  typedef union {
    S_Velocity velocity;
    S_Position position;
    S_Parameter parameter;
    S_Pause pause;
    S_SetMode mode;
  } MsgData;
  MsgData *msgdata;
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

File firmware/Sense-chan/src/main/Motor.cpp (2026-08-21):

#include "Motor.h"
#include <MP.h>

// モータ制御用サブコアID
const int SUBCORE_MOTOR = 1;

// メッセージID定義
const int8_t MSGID_BEGUN = 1;
const int8_t MSGID_SET_PARAMETER = 2;
const int8_t MSGID_SET_VELOCITY_MODE = 3;
const int8_t MSGID_SET_POSITION_MODE = 4;
const int8_t MSGID_SET_VELOCITY = 5;
const int8_t MSGID_SET_POSITION = 6;
const int8_t MSGID_SET_PAUSE = 7;
const int8_t MSGID_SET_MODE = 8;

// 初期化
void Motor::begin()
{
    // モータ制御用のサブコア起動
    int ret = MP.begin(SUBCORE_MOTOR);
    if (ret < 0) {
        Serial.printf("Motor: MP.begin error = %d\n", ret);
    }
    // サブコアの起動完了待ち
    MP.RecvTimeout(MP_RECV_BLOCKING);
    int8_t msgid;
    MP.Recv(&msgid, &_status, SUBCORE_MOTOR);
    if (msgid != MSGID_BEGUN) {
        Serial.printf("Motor: MP.Recv error: no BEGUN message %d\n", msgid);
    }

    // パラメータ設定
    uint32_t dummy = 0;
    MP.Send(MSGID_SET_PARAMETER, &parameter, SUBCORE_MOTOR);
    MP.Recv(&msgid, &dummy, SUBCORE_MOTOR);
    if (msgid != MSGID_SET_PARAMETER) {
        Serial.printf("Motor: MP.Recv error: no SET_PARAMETER message %d\n", msgid);
    }

    // 受信をポーリングに変更
    MP.RecvTimeout(MP_RECV_POLLING);
}

// メインループ処理
void Motor::loop()
{
    ; // 現状は特に何もしない
}

// 制御パラメータを設定
void Motor::setParameter()
{
    MP.Send(MSGID_SET_PARAMETER, &parameter, SUBCORE_MOTOR);
}

// 速度制御モードに設定
void Motor::setVelocityMode()
{
    uint32_t dummy = 0;
    MP.Send(MSGID_SET_VELOCITY_MODE, dummy, SUBCORE_MOTOR);
}

// 位置制御モードに設定
void Motor::setPositionMode()
{
    uint32_t dummy = 0;
    MP.Send(MSGID_SET_POSITION_MODE, dummy, SUBCORE_MOTOR);
}

// 速度の目標値を設定
void Motor::setVelocity(float l, float r)
{
    static struct {
        float l;
        float r;
    } msgdata;
    msgdata.l = l;
    msgdata.r = r;
    MP.Send(MSGID_SET_VELOCITY, &msgdata, SUBCORE_MOTOR);
}

// 位置の目標値を設定
void Motor::setPosition(float x, float y)
{
    static struct {
        float x;
        float y;
    } msgdata;
    msgdata.x = x;
    msgdata.y = y;
    MP.Send(MSGID_SET_POSITION, &msgdata, SUBCORE_MOTOR);
}

// 一時停止する
// pause : true:一時停止 / false:解除
void Motor::setPause(bool pause)
{
    static struct {
        bool pause;
    } msgdata;
    msgdata.pause = pause;

    MP.Send(MSGID_SET_PAUSE, &msgdata, SUBCORE_MOTOR);
    _pausing = pause;
}

// モード設定
// mode : モード
void Motor::setMode(int mode)
{
    static struct {
        int mode;
    } msgdata;
    msgdata.mode = mode;

    MP.Send(MSGID_SET_MODE, &msgdata, SUBCORE_MOTOR);
}

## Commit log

2025-12-13 add teardrops to PCB pattern
    [Sense-chan.kicad_pcb]
2025-12-13 modify PCB pattern
    [Sense-chan.kicad_pcb]
2025-12-13 add Gerber files
2025-12-28 add mechanical data
    [Body.step, Body.stl, LegL.step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]
2026-01-01 add screw list
    [screw_list.xlsx]
2026-01-01 modify screw list
    [screw_list.xlsx]
2026-01-07 modify 3D model data
    [Body.step, Body.stl, RearBracket.step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]
2026-01-07 modify mechanical design materials
    [screw_list.xlsx]
2026-01-20 add battery check
2026-04-16 Avatar -> MainCore, Motor -> SubCore1
2026-04-17 bug fix & enable VoiceDetector
    [main.cpp]
